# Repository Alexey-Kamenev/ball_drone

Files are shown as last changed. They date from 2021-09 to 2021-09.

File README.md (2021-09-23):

# Ball drone assembly notes

Based on [this](https://hackaday.io/project/175512-the-ball-drone-project-mk-ii) project with very slight modifications.

## Parts

**Note**: you only need **one** receiver from the list below, depending on your transmitter. See details [here](https://www.rcgroups.com/forums/showthread.php?2301242-The-Beginners-Guide-to-RC-Protocols) or [here](http://openpanzer.org/wiki/doku.php?id=wiki:tcb:tcbinstall:rx:rxselection).

| Name | Comments | Price $ |
| ---- | --- | ----- |
| 3D printed [parts](./3d_printing) | Had to modify a bit (rotate / slice) to be able to print on Prusa i3 MK2 | - |
| Flight controller [Mamba MK2 F405](https://www.diatone.us/collections/basic-fc/products/mamba-f405-flight-controller-mk2) | [Banggood](https://www.banggood.com/search/1345007.html) - was out of stock | 27.55 |
| RC receiver [Flysky FS-A8S](https://www.banggood.com/search/1092861.html) | For FlySky (AFHDS 2A) transmitters |  11.99 |
| RC receiver [FrSky R-XSR](https://www.amazon.com/FrSky-R-XSR-Redundancy-Telemetry-Receiver/dp/B074QHJRBC) | For FrSky (ACCST) transmitters (e.g. Taranis) |  25.59 |
| ESC [T-motor F35A 3-6S BLHeli_32](https://www.banggood.com/search/1221106.html) | Alternative: [DYS BL30A Mini 30A BLHeli OPTO](https://www.banggood.com/search/975799.html)  | 22 |
| Motors [Racerstar Racing Edition 2306](https://www.banggood.com/search/1149532.html) | - | 9.60 |
| Propeller [FCMODEL 6045 6 Inch 3-Blade](https://www.banggood.com/search/1006366.html) | - | 3.49 |
| Servos [4X Emax ES9051 Digital Mini Servo](https://www.banggood.com/search/1039587.html) | - | 16.99 |
| Battery [Tattu 11.1V 1300mAh 75C 3S](https://www.amazon.com/1300mAh-Battery-Airplane-Shredder-HOVERSHIP/dp/B013I9SYC0/) | - | 18.99 |
| M3 [hardware kit](https://www.amazon.com/SZHKM-Screws-Washer-Varied-Assortment/dp/B076J5RGKS/) | Nylon instead of metal | 14.99 |
| Servo [extension cables](https://www.amazon.com/gp/product/B00MIQRN2C) | Needed as an extension to connect servos to FC | 5.99 |
| XT60 [male connector](https://www.amazon.com/MCIGICM-Female-Bullet-Connectors-Battery/dp/B07DVDKL42/) | - | |

## Assembly

Follow the instructions on [Hack-A-Day](https://hackaday.io/project/175512-the-ball-drone-project-mk-ii) or [Make Magazine, Vol. 76](https://makezine.com/).

### Servo calibration

To center the servos you can use provided [Arduino sketch](./sketches/servo_calib.ino).
Here is the respective wiring:

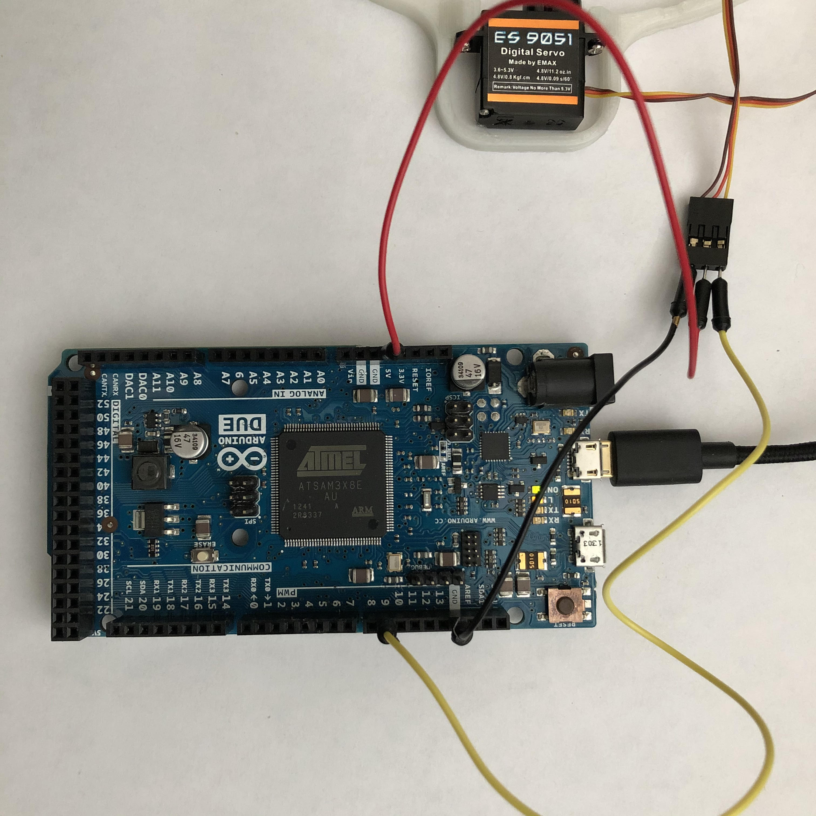
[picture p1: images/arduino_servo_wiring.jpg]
Arduino Servo Wiring


### RC Receiver binding

Binding RC transmitter and receiver can sometimes be tricky. Most importantly, make sure that protocols, AFHDS or ACCST, of transmitter and receiver match.

In my case, I have [Taranis X9D+](https://www.frsky-rc.com/product/taranis-x9d-plus-2/) transmitter and [FrSky R-XSR](https://www.frsky-rc.com/r-xsr/) receiver. My firmware configuration is:
* [OpenTX 2.3.11](https://www.open-tx.org/2021/01/08/opentx-2.3.11). How to [update](https://oscarliang.com/flash-opentx-firmware-taranis/).
* Pre 2.x version of firmware both in Taranis XJT internal module and R-XSR receiver (ACCST D16).
    * It is important that these versions match, otherwise transmitter and receiver will not bind.
    * [How to update receiver firmware](https://www.frsky-rc.com/how-to-use-the-transmitter-to-flash-the-firmware-of-the-x8r-receiver/), or [another tutorial](https://oscarliang.com/flash-frsky-rx-firmware/).
    * [XJT firmware](https://www.frsky-rc.com/xjt/)
    * If you decide to use version 2.x, then corresponding matching versions need to be flashed both in transmitter XJT module and receiver.

## Configuring Betaflight

### Resource Remapping
First you need to remap servos to 4 standard motor outputs and our motor output to PPM.
Open **CLI** tab in Betaflight and run the following:

```
resource MOTOR 1 NONE
resource MOTOR 2 NONE
resource MOTOR 3 NONE
resource MOTOR 4 NONE

resource PPM 1 NONE

resource SERVO 1 A03
resource SERVO 2 B01
resource SERVO 3 B00
resource SERVO 4 A02

resource MOTOR 1 C09

save
```

```
# resource MOTOR 1 C09

NOTE: C09 already assigned to ESCSERIAL.

Resource is set to C09
```

### Mixer

```
# smix script for singlecopter on MambaF405_MK2 (by Benjamin Prescher)
mixer CUSTOMAIRPLANE

# load a standard motor mix
mmix reset
mmix load airplane    # Motor1 as ESC output
#mmix 0  1.000  0.000  0.000  0.000

# smix
smix reset
smix 0 3 0  100 0 0 100 0
smix 1 2 0 -100 0 0 100 0
smix 2 4 1  100 0 0 100 0
smix 3 5 1 -100 0 0 100 0
smix 4 3 2 50 0 0 100 0
smix 5 2 2 50 0 0 100 0
smix 6 4 2 50 0 0 100 0
smix 7 5 2 50 0 0 100 0
save
```

### Servos config

1. In Configuration tab, set **PID loop frequency** under **System Configuration** section to 1KHz.
2. Update servo LPF:
    ```
    set servo_lowpass_hz = 20
    set servo_pwm_rate = 250
    save
    ```

## Final check

Do not forget to check propeller rotation! Re-solder the wires (swap any 2 ESC-motor wires) if needed.

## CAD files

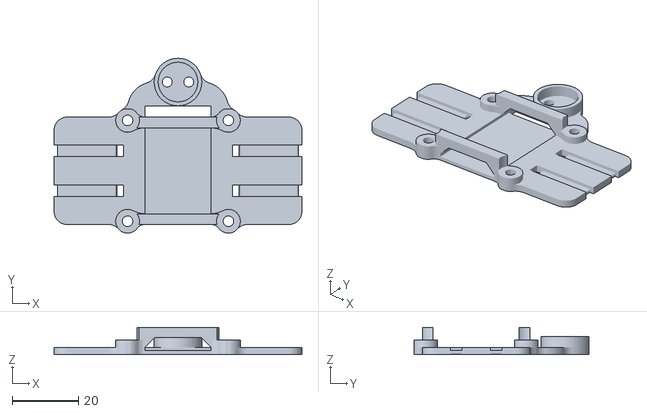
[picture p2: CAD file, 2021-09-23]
3d_printing/files/batBuzHolder.stl
75.0 x 52.8 x 8.20

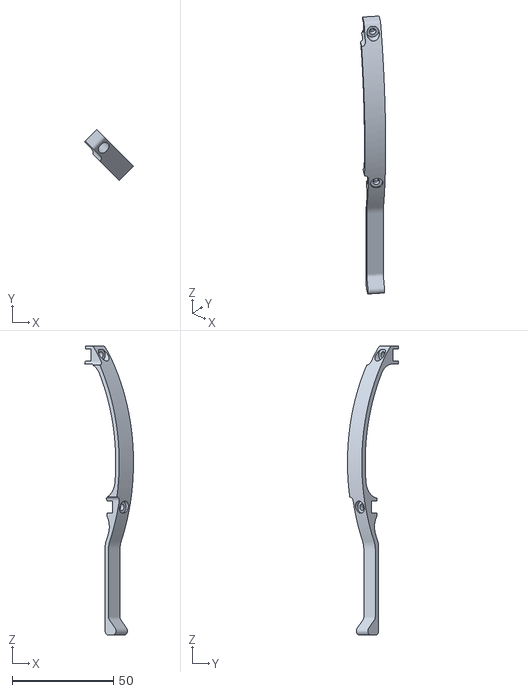
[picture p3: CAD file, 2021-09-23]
3d_printing/files/leg_4x.stl
24.2 x 25.2 x 142.4

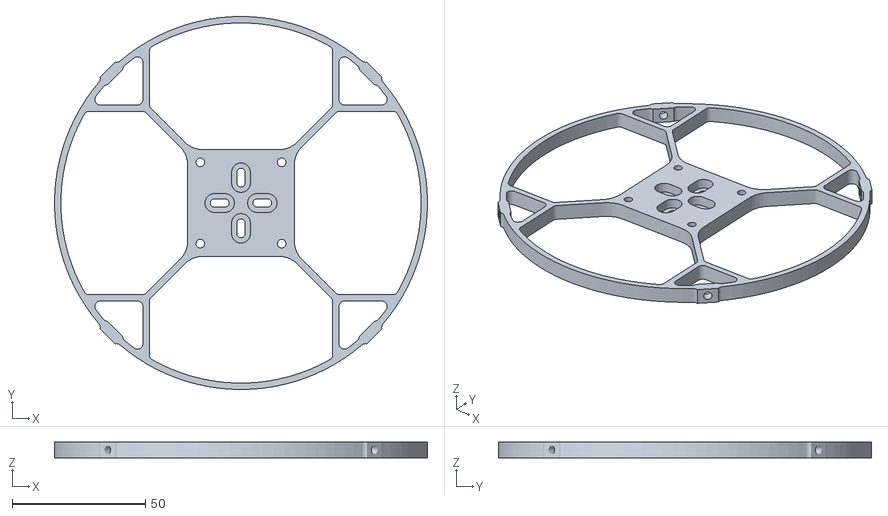
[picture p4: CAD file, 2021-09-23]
3d_printing/files/upperRing.stl
140.0 x 140.0 x 6.00

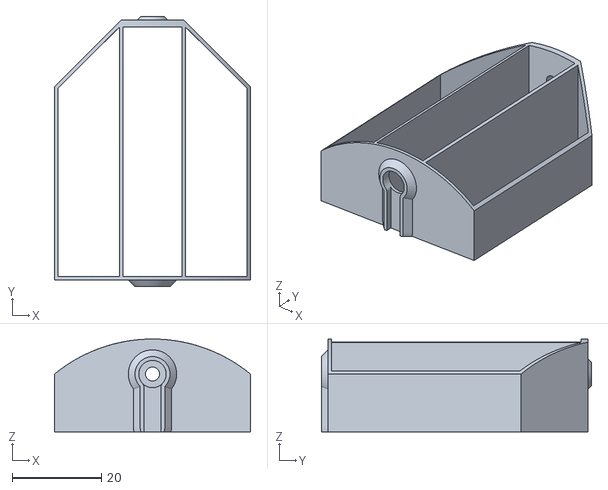
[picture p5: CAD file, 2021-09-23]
3d_printing/files/vane_4x.stl
44.0 x 60.7 x 20.9

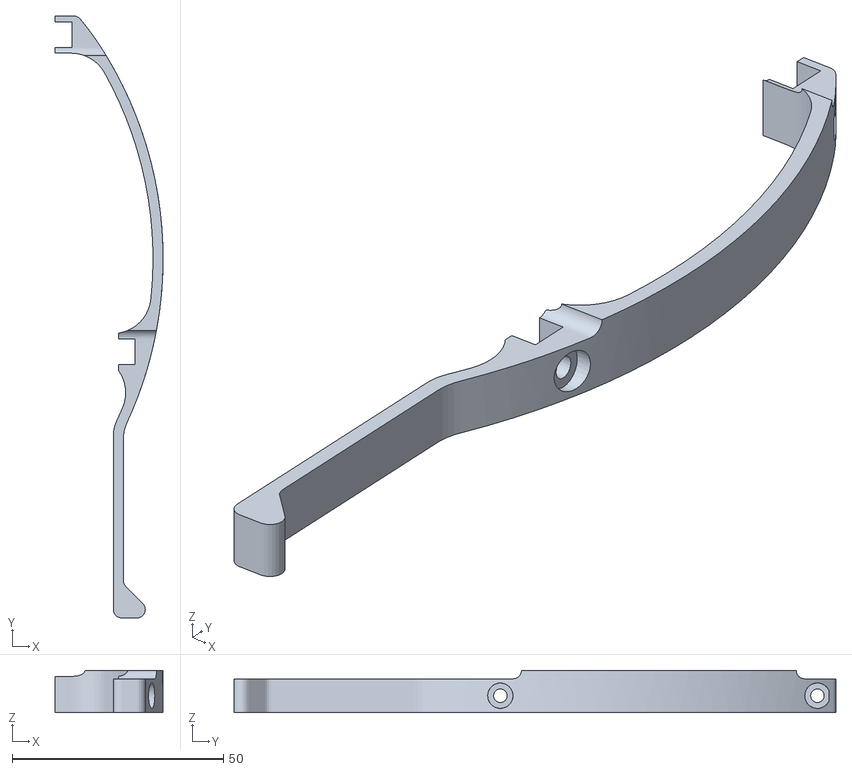
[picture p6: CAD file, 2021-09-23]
3d_printing/files/leg_4x_flat.stl
25.6 x 142.4 x 10.0

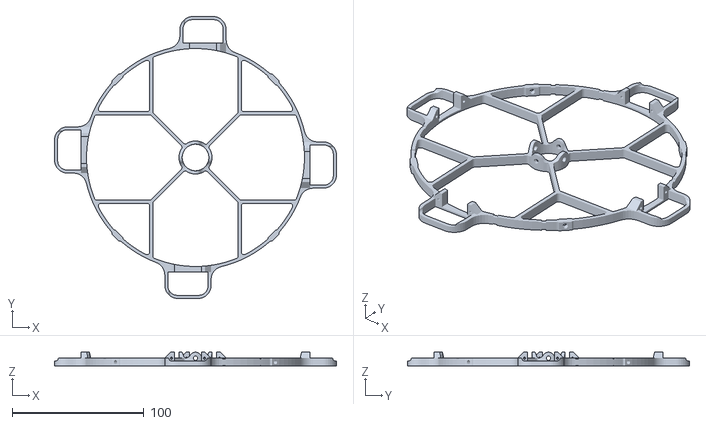
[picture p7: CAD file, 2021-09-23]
3d_printing/files/lowerRing.stl
213.8 x 213.8 x 10.8

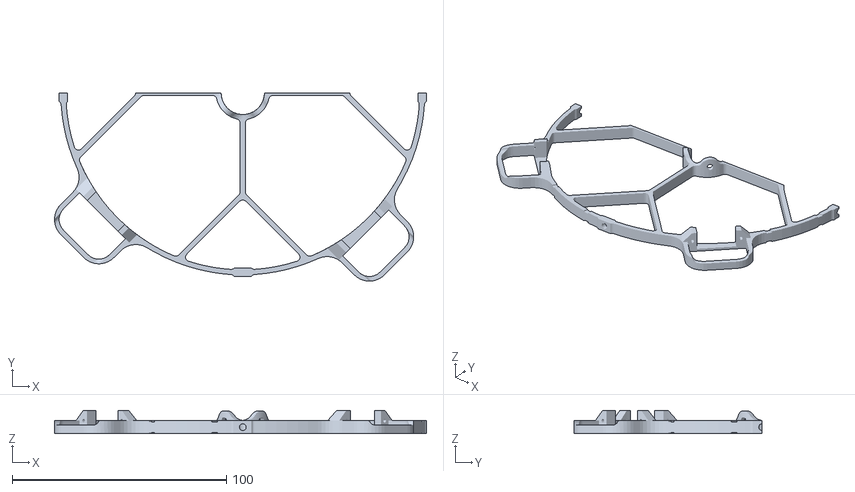
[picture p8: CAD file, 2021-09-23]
3d_printing/files/lowerRing_half.stl
173.7 x 87.9 x 10.8

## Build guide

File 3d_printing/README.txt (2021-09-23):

Ball Drone MK II by Ben5en on Thingiverse: https://www.thingiverse.com/thing:4635873

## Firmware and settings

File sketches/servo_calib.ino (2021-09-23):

#include <Servo.h>

Servo s;     // create servo object to control the servos.

// Servo range is 0-180, so 90 is the middle value that corresponds to 1.5ms pulse.
int mid = 90;

void setup() {
  // Attach the servo on pin 9
  s.attach(9, 1000, 2000); // (pin, min pulse width, max pulse width in microseconds) 
}

void loop() {
  s.write(mid);
}
